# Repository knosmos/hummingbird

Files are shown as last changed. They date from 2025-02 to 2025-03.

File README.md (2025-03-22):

<picture>
  <source media="(prefers-color-scheme: dark)" srcset="https://github.com/user-attachments/assets/7356b551-4785-46c3-8079-baab0482c5df">
  <source media="(prefers-color-scheme: light)" srcset="https://github.com/user-attachments/assets/484456df-929e-4e9f-abab-7f0c61837f22">
  hummingbird
</picture>

Custom STM32 flight controller for MIT Design Build Fly 2025

### Features

- STM32F103C8T6 microprocessor
- Altimeter and IMU
- 2x Servo PWM
- 12V / 5V LDO regulators
- MOSFET LED drive circuits
- Hall effect sensor input
- GPS and magnetometer input

### Layout


### Schematic


### Renderings


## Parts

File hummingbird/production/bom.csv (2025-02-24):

Designator | Footprint | Quantity | Value | LCSC Part #
C1, C11, C12, C4, C5, C6, C7 | 0402 | 7 | 100n | C1525
C10 | 0402 | 1 | 2u2 | C12530
C13, C8 | 0805 | 2 | 22u | C45783
C14, C9 | 0603 | 2 | 22u | C59461
C15 | 0402 | 1 | 4u7 | C23733
C17 | 0402 | 1 | 10n | C15195
C18, C19 | 0402 | 2 | 1u | C52923
C2, C3 | 0402 | 2 | 15p | C1548
D1 | 0603 | 1 | LED | C2286
FB1 | 0805 | 1 | 100 | C1015
J1 | USB_C_Receptacle_GCT_USB4105-xx-A_16P_TopMnt_Horizontal | 1 | USB_C_Receptacle_USB2.0_16P | C2765186
J2 | PinHeader_1x03_P2.54mm_Horizontal | 1 | srv1
J3 | PinHeader_1x03_P2.54mm_Horizontal | 1 | srv2
J4 | PinHeader_1x03_P2.54mm_Horizontal | 1 | halleffect
J5 | JST_SH_SM06B-SRSS-TB_1x06-1MP_P1.00mm_Horizontal | 1 | Conn_01x06 | C3029345
J6, J7 | SolderWire-0.1sqmm_1x02_P3.6mm_D0.4mm_OD1mm | 2 | Conn_01x02
J8 | PinHeader_2x01_P2.54mm_Vertical | 1 | PWR_IN
J9 | PinHeader_2x02_P2.54mm_Vertical | 1 | Conn_02x02_Counter_Clockwise
Q1, Q2 | SOT-23 | 2 | AO3400A | C20917
R1, R4, R5 | 0402 | 3 | 10k | C25744
R2, R3, R6 | 0402 | 3 | 5k1 | C25905
U1 | LQFP-48_7x7mm_P0.5mm | 1 | STM32F103C8Tx
U2 | SOT-223-3_TabPin2 | 1 | AMS1117-3.3 | C6186
U3 | LGA-14_3x2.5mm_P0.5mm_LayoutBorder3x4y | 1 | ICM-42688-P | C1850418
U4 | SOT-223-3_TabPin2 | 1 | AMS1117-5 | C6187
U5 | QFN (3.8x3.8) | 1 | ~ | C138665
Y1 | Crystal_SMD_3225-4Pin_3.2x2.5mm | 1 | 16mhz | C13738

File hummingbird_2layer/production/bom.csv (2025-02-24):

Designator | Footprint | Quantity | Value | LCSC Part #
C1, C11, C12, C21, C4, C5, C6, C7 | 0402 | 8 | 100n | C1525
C10 | 0402 | 1 | 2u2 | C12530
C13, C8 | 0805 | 2 | 22u | C45783
C14, C9 | 0603 | 2 | 22u | C59461
C17 | 0402 | 1 | 10n | C15195
C18, C19 | 0402 | 2 | 1u | C52923
C2, C3 | 0402 | 2 | 15p | C1548
C20 | 0402 | 1 | 4u7 | C23733
D1 | 0603 | 1 | LED | C2286
FB1 | 0805 | 1 | 100 | C1015
J1 | USB_C_Receptacle_GCT_USB4105-xx-A_16P_TopMnt_Horizontal | 1 | USB_C_Receptacle_USB2.0_16P | C2765186
J2 | PinHeader_1x03_P2.54mm_Horizontal | 1 | srv1
J3 | PinHeader_1x03_P2.54mm_Horizontal | 1 | srv2
J4 | PinHeader_1x03_P2.54mm_Horizontal | 1 | halleffect
J5 | JST_SH_SM06B-SRSS-TB_1x06-1MP_P1.00mm_Horizontal | 1 | Conn_01x06 | C22461268
J6, J7 | SolderWire-0.1sqmm_1x02_P3.6mm_D0.4mm_OD1mm | 2 | Conn_01x02
J8 | PinHeader_2x01_P2.54mm_Vertical | 1 | PWR_IN
J9 | PinHeader_2x02_P2.54mm_Vertical | 1 | Conn_02x02_Counter_Clockwise
Q1, Q2 | SOT-23 | 2 | AO3400A | C20917
R2, R3, R6 | 0402 | 3 | 5k1 | C25905
R5 | 0402 | 1 | 10k | C25744
U1 | LQFP-48_7x7mm_P0.5mm | 1 | STM32F103C8Tx
U2 | SOT-223-3_TabPin2 | 1 | AMS1117-3.3 | C6186
U3 | LGA-14_3x2.5mm_P0.5mm_LayoutBorder3x4y | 1 | ICM-42688-P | C1850418
U4 | SOT-223-3_TabPin2 | 1 | AMS1117-5 | C6187
U6 | ST_HLGA-10_2x2mm_P0.5mm_LayoutBorder3x2y | 1 | LPS22HH | C2827824
Y1 | Crystal_SMD_3225-4Pin_3.2x2.5mm | 1 | 16mhz | C13738

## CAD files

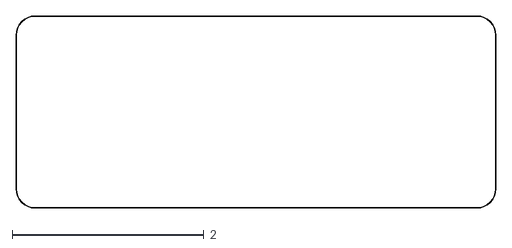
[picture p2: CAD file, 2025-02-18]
hummingbird_2layer/hummingbird_shape.dxf
5.00 x 2.00

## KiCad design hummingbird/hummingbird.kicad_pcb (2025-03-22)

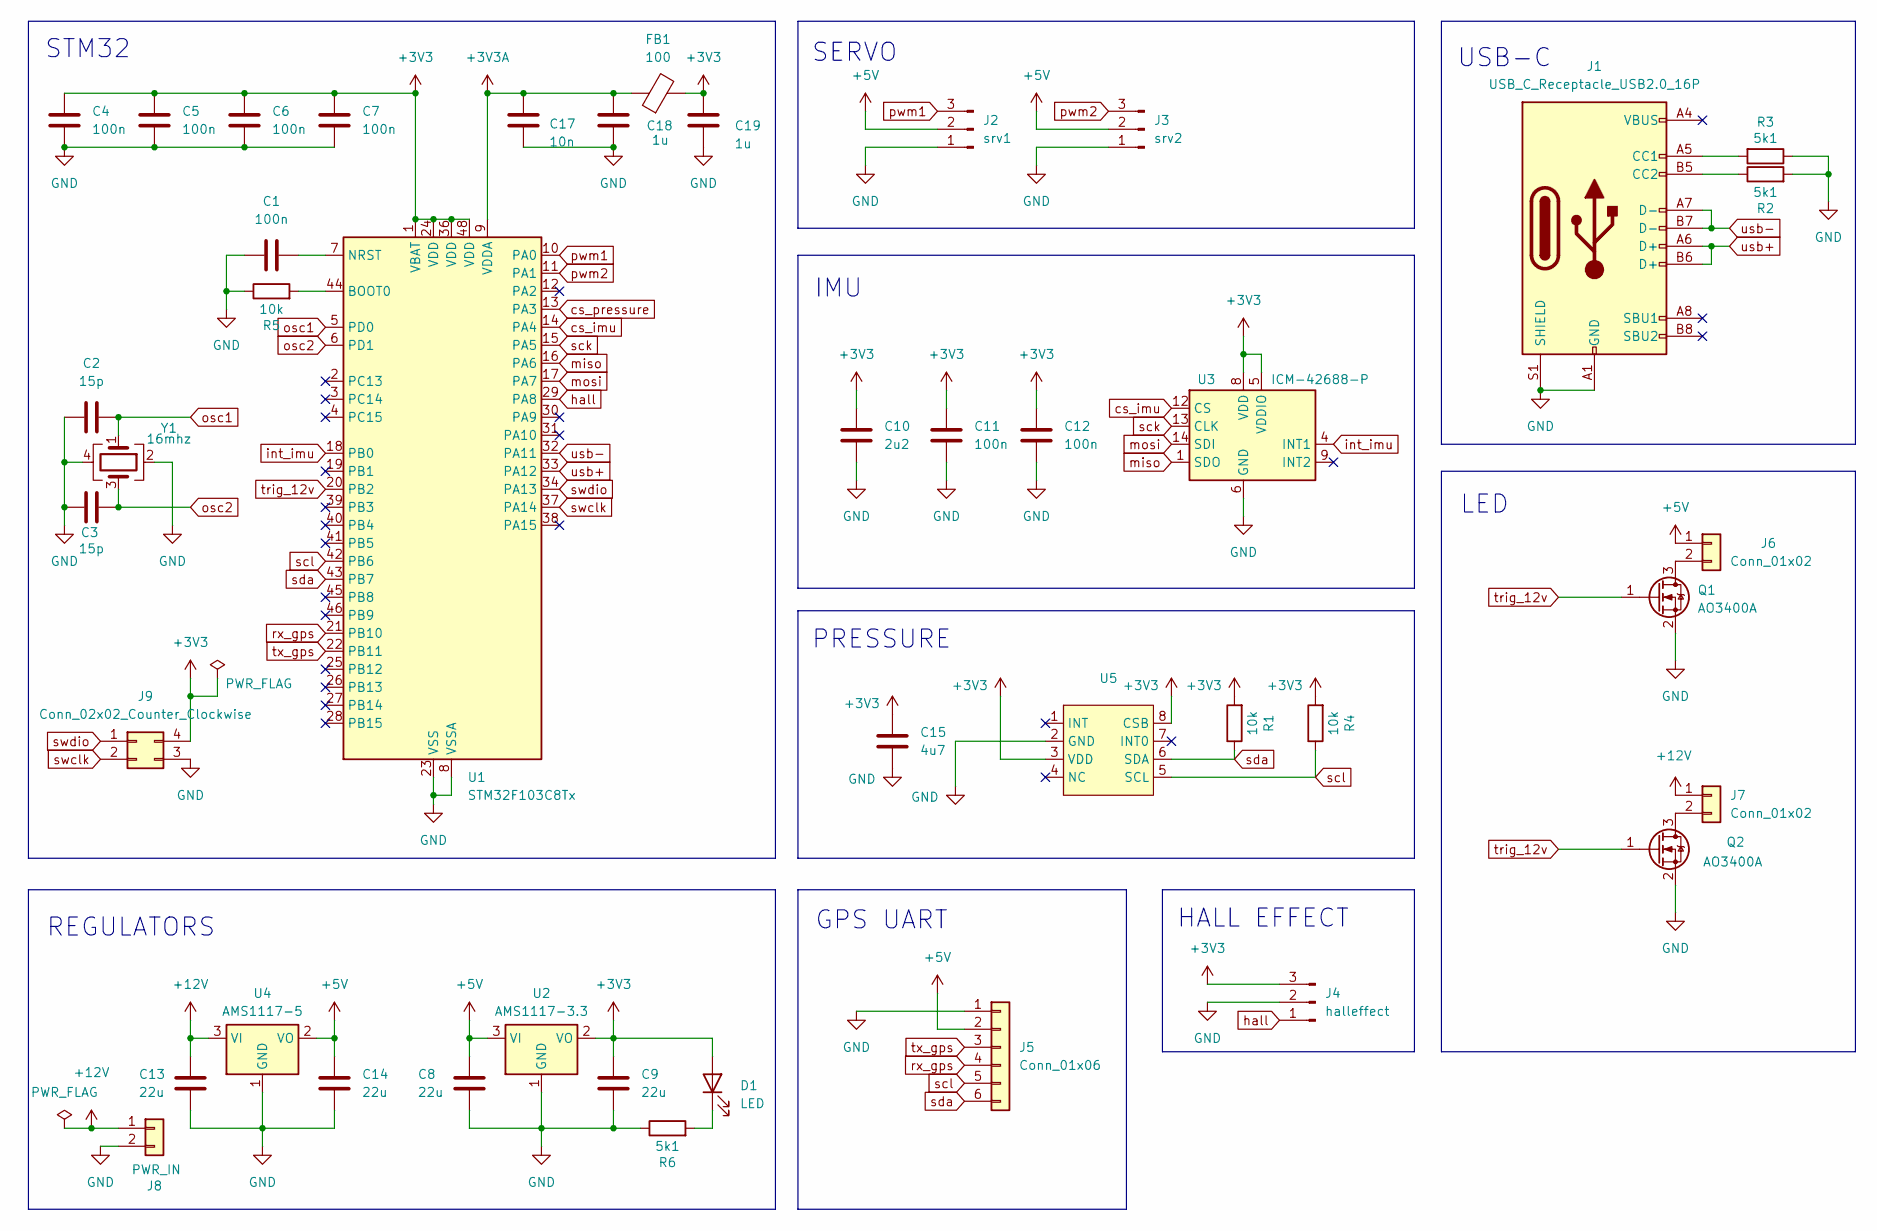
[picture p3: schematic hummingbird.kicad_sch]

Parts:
C1, C4, C5, C6, C7, C11, C12: 100n; C_0402_1005Metric; LCSC C1525
C2, C3: 15p; C_0402_1005Metric; LCSC C1548
C8, C13: 22u; C_0805_2012Metric; LCSC C45783
C9, C14: 22u; C_0603_1608Metric; LCSC C59461
C10: 2u2; C_0402_1005Metric; LCSC C12530
C15: 4u7; C_0402_1005Metric; LCSC C23733
C17: 10n; C_0402_1005Metric; LCSC C15195
C18, C19: 1u; C_0402_1005Metric; LCSC C52923
D1: LED; LED_0603_1608Metric; LCSC C2286
FB1: 100; L_0805_2012Metric; LCSC C1015
J1: USB_C_Receptacle_USB2.0_16P; USB_C_Receptacle_GCT_USB4105-xx-A_16P_TopMnt_Horizontal; LCSC C2765186
J2: srv1; PinHeader_1x03_P2.54mm_Horizontal
J3: srv2; PinHeader_1x03_P2.54mm_Horizontal
J4: halleffect; PinHeader_1x03_P2.54mm_Horizontal
J5: Conn_01x06; JST_SH_SM06B-SRSS-TB_1x06-1MP_P1.00mm_Horizontal
J6, J7: Conn_01x02; SolderWire-0.1sqmm_1x02_P3.6mm_D0.4mm_OD1mm
J8: PWR_IN; PinHeader_2x01_P2.54mm_Vertical
J9: Conn_02x02_Counter_Clockwise; PinHeader_2x02_P2.54mm_Vertical
Q1, Q2: AO3400A; SOT-23; LCSC C20917
R1, R4, R5: 10k; R_0402_1005Metric; LCSC C25744
R2, R3, R6: 5k1; R_0402_1005Metric; LCSC C25905
U1: STM32F103C8Tx; LQFP-48_7x7mm_P0.5mm
U2: AMS1117-3.3; SOT-223-3_TabPin2; LCSC C6186
U3: ICM-42688-P; LGA-14_3x2.5mm_P0.5mm_LayoutBorder3x4y; LCSC C1850418
U4: AMS1117-5; SOT-223-3_TabPin2; LCSC C6187
U5: QFN (3.8x3.8); LCSC C138665
Y1: 16mhz; Crystal_SMD_3225-4Pin_3.2x2.5mm; LCSC C13738

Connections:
+3V3: C4.2, C5.2, C6.2, C7.2, C9.1, C10.1, C11.1, C12.1, C15.1, C19.1, D1.2 (A), FB1.2, J4.3, J9.4, R1.2, R4.2, U1.1 (VBAT), U1.24 (VDD), U1.36 (VDD), U1.48 (VDD), U2.2 (VO), U3.5 (VDDIO), U3.8 (VDD), U5.3 (VDD), U5.8 (CSB)
+3V3A: C17.1, C18.1, FB1.1, U1.9 (VDDA)
+5V: C8.1, C14.1, J2.2, J3.2, J5.2, J6.1, U2.3 (VI), U4.2 (VO)
+12V: C13.1, J7.1, J8.1, U4.3 (VI)
GND: C1.1, C2.1, C3.1, C4.1, C5.1, C6.1, C7.1, C8.2, C9.2, C10.2, C11.2, C12.2, C13.2, C14.2, C15.2, C17.2, C18.2, C19.2, J1.A1 (GND), J1.A12 (GND), J1.B1 (GND), J1.B12 (GND), J1.S1 (SHIELD), J2.1, J3.1, J4.2, J5.1, J8.2, J9.3, Q1.2 (S), Q2.2 (S), R2.2, R3.1, R5.1, R6.1, U1.8 (VSSA), U1.23 (VSS), U1.35 (VSS), U1.47 (VSS), U2.1 (GND), U3.6 (GND), U3.7 (RESV), U3.11 (RESV), U4.1 (GND), U5.2 (GND), Y1.2, Y1.4
unnamed: D1.1 (K), R6.2
unnamed: J1.A5 (CC1), R3.2
unnamed: J1.B5 (CC2), R2.1
unnamed: J6.2, Q1.3 (D)
unnamed: J7.2, Q2.3 (D)
unnamed: R5.2, U1.44 (BOOT0)
unnamed: C1.2, U1.7 (NRST)
cs_imu: U1.14 (PA4), U3.12 (CS)
cs_pressure: U1.13 (PA3)
hall: J4.1, U1.29 (PA8)
int_imu: U1.18 (PB0), U3.4 (INT1)
miso: U1.16 (PA6), U3.1 (SDO)
mosi: U1.17 (PA7), U3.14 (SDI)
osc1: C2.2, U1.5 (PD0), Y1.1
osc2: C3.2, U1.6 (PD1), Y1.3
pwm1: J2.3, U1.10 (PA0)
pwm2: J3.3, U1.11 (PA1)
rx_gps: J5.4, U1.21 (PB10)
sck: U1.15 (PA5), U3.13 (CLK)
scl: J5.5, R4.1, U1.42 (PB6), U5.5 (SCL)
sda: J5.6, R1.1, U1.43 (PB7), U5.6 (SDA)
swclk: J9.2, U1.37 (PA14)
swdio: J9.1, U1.34 (PA13)
trig_12v: Q1.1 (G), Q2.1 (G), U1.20 (PB2)
tx_gps: J5.3, U1.22 (PB11)
usb+: J1.A6 (D+), J1.B6 (D+), U1.33 (PA12)
usb-: J1.A7 (D-), J1.B7 (D-), U1.32 (PA11)

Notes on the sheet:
LED
HALL EFFECT
REGULATORS
USB-C
SERVO
IMU
PRESSURE
STM32
GPS UART

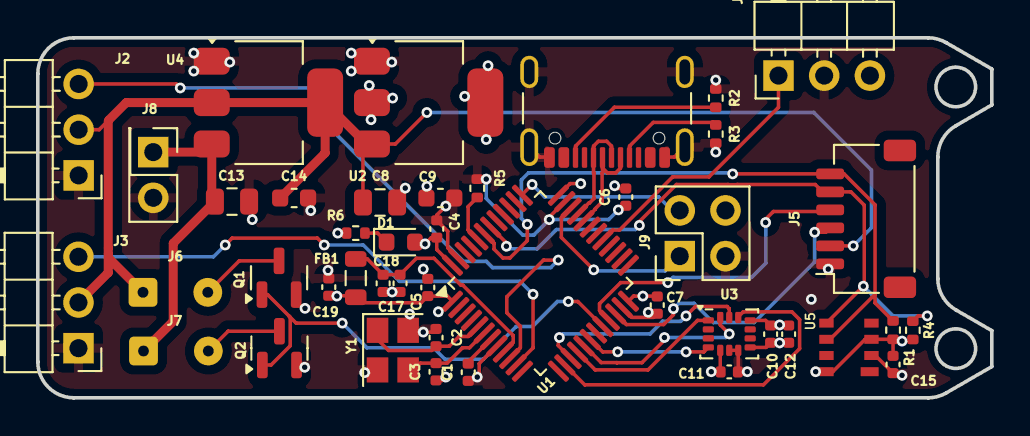
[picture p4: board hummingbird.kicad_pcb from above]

Board: 4 copper layers, 53.0 x 20.0 mm, 43 parts (0 on the bottom side), 31 nets.

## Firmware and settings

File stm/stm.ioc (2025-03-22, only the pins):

Mcu.UserName=STM32F103C8Tx
PA0-WKUP.Signal=S_TIM2_CH1_ETR
PA11.Signal=USB_DM
PA12.Signal=USB_DP
PA13.Signal=SYS_JTMS-SWDIO
PA14.Signal=SYS_JTCK-SWCLK
PA3.Signal=GPIO_Output
PA4.Signal=GPIO_Output
PA5.Signal=SPI1_SCK
PA6.Signal=SPI1_MISO
PA7.Signal=SPI1_MOSI
PA8.Signal=GPIO_Input
PB10.Signal=USART3_TX
PB11.Signal=USART3_RX
PB2.Signal=GPIO_Output
PB6.Signal=I2C1_SCL
PB7.Signal=I2C1_SDA
PD0-OSC_IN.Signal=RCC_OSC_IN
PD1-OSC_OUT.Signal=RCC_OSC_OUT

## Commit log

2025-02-24 backup before replacing sensor
    [bom.csv, designators.csv, hummingbird.kicad_pcb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]
2025-02-24 completion, may have usbc placement bug
    [bom.csv, designators.csv, hummingbird.kicad_pcb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]
2025-03-22 Add STM32 skeleton code
    [hummingbird.kicad_pcb]
